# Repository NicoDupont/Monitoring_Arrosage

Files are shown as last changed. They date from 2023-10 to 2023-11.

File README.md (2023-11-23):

## Monitoring du circuit d'eau d'arrosage

# Montage réalisé sur une protoboard. un pcb dédié sera réalisé

Montage à base d'esp32 utilisé principalement pour monitorer le circuit d'arrosage.  

- pression
- temperature
- debitmetre/volume
- Ouverture/fermeture vanne motorisée  

### Fonctionnement :

Collecte des données.  
Les données remontent dans home-assistant via esphome.  
 => automatisme dans home-assistant   

### Liste des composants :

- 1x esp32 avec antenne wifi externe soudée sur connecteur sma (pas d'esp32u sous la main)
- 8x relais 5v (2x4) (alimente en 5v, logique en 3.3v)
- 1x alim 12v2A
- 1x convertisseur dc 12v=>5v
- 1x convertisseur dc 5v=>3.3v (ams1117)
- 2x BME280 (3.3v)
- 2x DS18B20 (3.3v)
- 1x resistance 4.7 Kohm
- 4x résistance 10 kohm
- 1x PCF8575 (3.3v)
- 1x ADS1115 (5v) + 1x level shifter (i2c 5v<=>3.3v)
- 3x Vannes motorisées 1" 12vdc avec retour d'info position (12v,cr702,bsp,manuel+indicateur) [vanne](https://fr.aliexpress.com/item/32960203891.html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)
- 3x Capteur pression 0.5/4.5v 0-100psi (5v) [pression](https://www.amazon.fr/gp/product/B08ZDLYKFH/ref=ox_sc_saved_image_1?smid=A1KGD9U4C0ZGWS&psc=1)
- 2 débimetres 1.5" YF-DN40 0-150L (5v) [debimetre](https://fr.aliexpress.com/item/1005003177939542.html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)
- Pcb, Bornier, Connecteur, entretoise, cavalier, support,Fusible, Porte Fusible, etc... 

### Cablage :

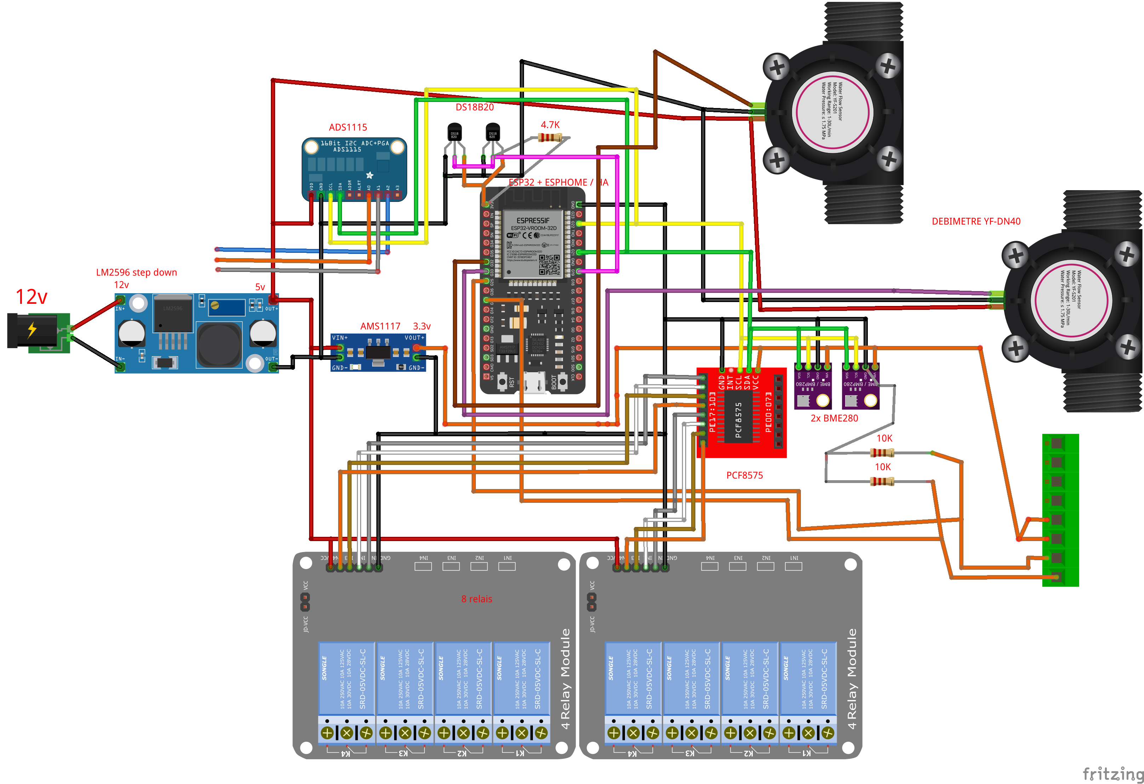
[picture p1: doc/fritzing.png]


### Montage :

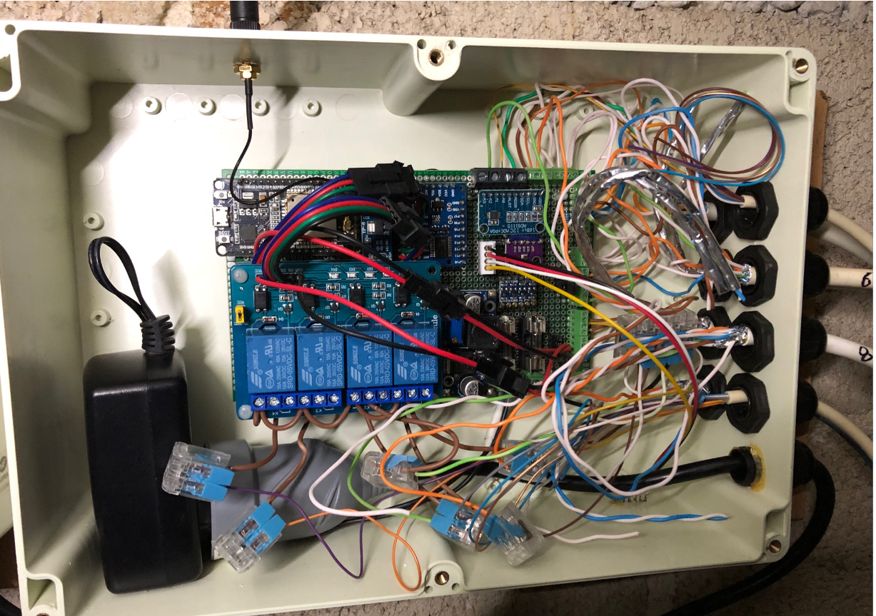
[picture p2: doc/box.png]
board


### HomeAssistant :

#### Esphome :

[yaml](https://github.com/NicoDupont/Monitoring_Arrosage/blob/main/esp-vs-arrosage.yaml)

#### Entités :

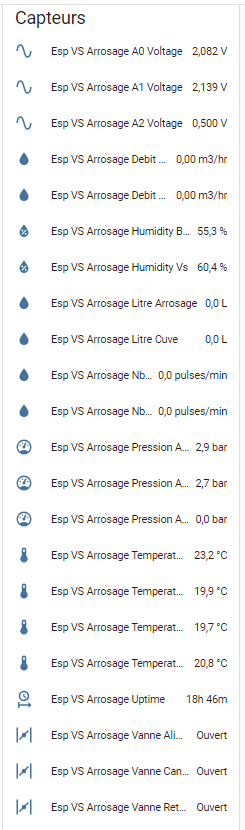
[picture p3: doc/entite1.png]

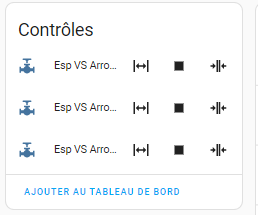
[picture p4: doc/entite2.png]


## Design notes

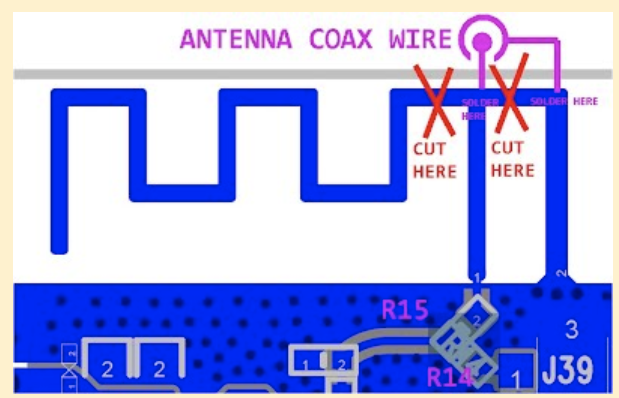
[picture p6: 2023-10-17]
doc/antenne_esp32.png

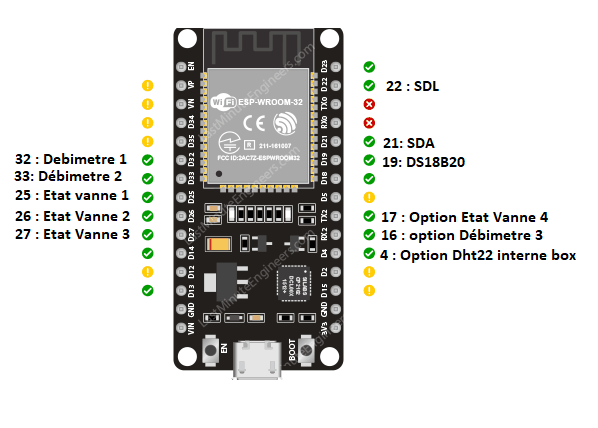
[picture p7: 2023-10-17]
doc/ESP32-GPIO-moni_arrosage.png

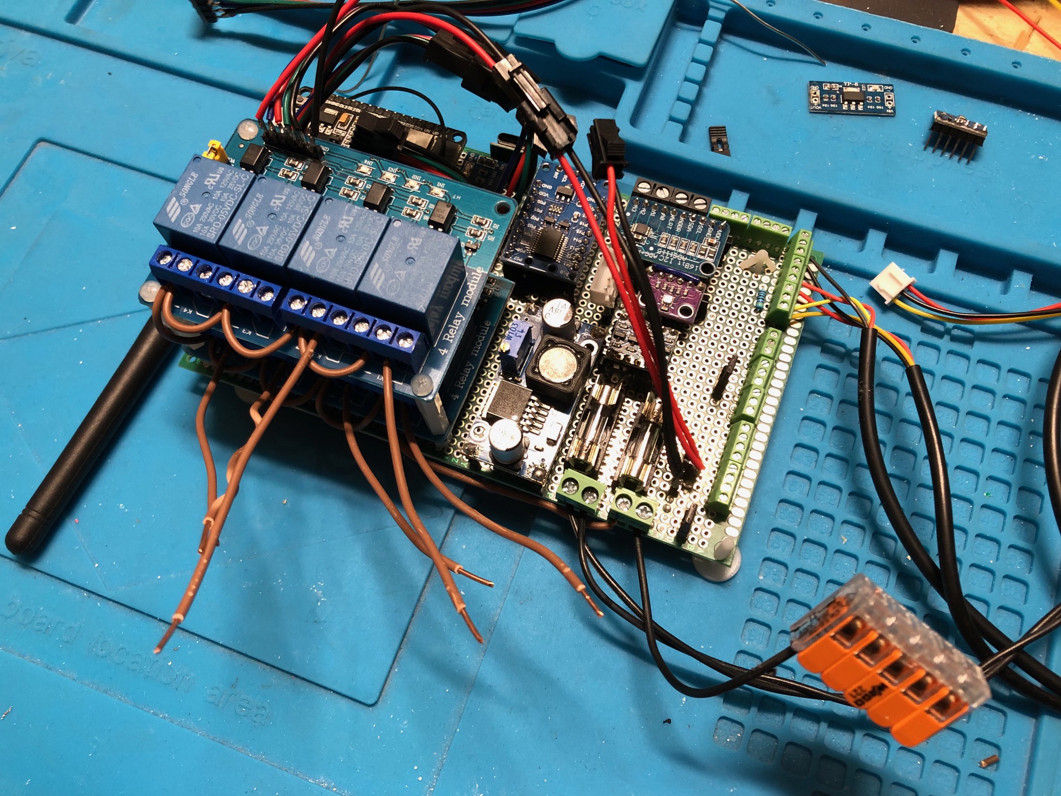
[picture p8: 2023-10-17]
doc/pcbok.jpg

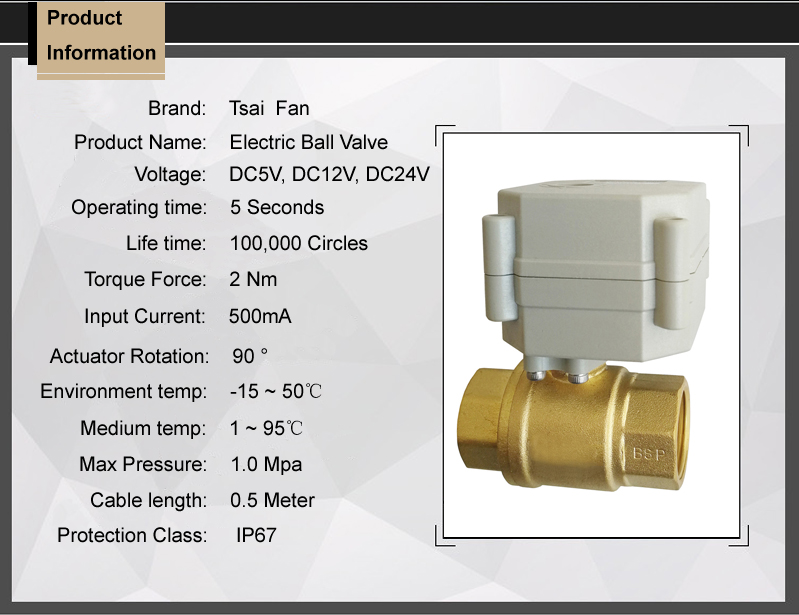
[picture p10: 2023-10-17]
doc/vanne1.jpg

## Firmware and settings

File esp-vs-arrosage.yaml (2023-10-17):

substitutions:
  friendly_name: "Esp VS Arrosage"
  friendly_name_wifiap: "Esp-VS-Arrosage-Hotspot"
  interval_update_court: "5s"
  interval_update_normal: "60s"
  interval_update_long: "600s"
  valve_duration: "5s"

esphome:
  name: esp-vs-arrosage
  comment: esp32 30pin monitoring temperature + pression + débimetre + gestion des vannes motorisées de la partie arrosage dans le vide sanitaire

esp32:
  board: esp32dev

# Enable logging
logger:

# Enable Home Assistant API
api:
#  encryption:
#    key: "a/cf+0bYDB1PlbJG8EkZfm23KiwYMVkIwHGuOpQmEqk="

ota:
  password: "001e0cad2c29a727973ae716dd966c53"

wifi:
  networks:
  - ssid: !secret wifi_maison_ssid
    password: !secret wifi_maison_password
  - ssid: !secret wifi_maison_2_ssid
    password: !secret wifi_maison_2_password
  reboot_timeout : 2min #reboot si pas de wifi actif

  # Enable fallback hotspot (captive portal) in case wifi connection fails
  ap:
    ssid: "${friendly_name_wifiap}"
    password: !secret wifi_esp_ap_password

captive_portal:

#--------------------------------------
#esp32_ble_tracker:
#bluetooth_proxy:

#--------------------------------------
web_server:
  port: 80
  version: 2

# ds18b20 temperature eau
dallas:
  - update_interval : ${interval_update_normal}
    pin: 19
    id: dallas_a
  
#i2c ads1115 + pcf8575 + bme280
i2c:
  sda: 21
  scl: 22
  scan: True
  id: bus_a

#i2c pcf8575 i/o extender 16 gpio pour gérer les 2 cartes 4 relais (3 vannes motorisées et donc 1 vanne possible en plus )
pcf8574:
  - id: 'pcf8575_hub'
    address: 0x20 #ou 0x21
    pcf8575: True

#i2c ads1115 pour lire les capteurs de pression 100psi 0.5=>4.5v
ads1115:
  - address: 0x48

time:
  - platform: homeassistant
    timezone: "Europe/Paris"
    id: ha_time

#----------------------------------------------------------------------------------------------
#----------------------------------------------------------------------------------------------
#binary_sensor
binary_sensor:

# ETAT VANNE MOTORISEE  
  - platform: gpio
    pin:
      number: 25
      inverted: true
    name: "${friendly_name} Vanne Canal Status"
    id: EspVsArrosageVanneCanalStatus
    device_class: opening

  - platform: gpio
    pin:
      number: 26
      inverted: true
    name: "${friendly_name} Vanne Alim Cuve Status"
    id: EspVsArrosageVanneAlimCuveStatus
    device_class: opening

  - platform: gpio
    pin:
      number: 27
      inverted: true
    name: "${friendly_name} Vanne Retour Cuve Status"
    id: EspVsArrosageVanneRetourCuveStatus
    device_class: opening

# DIAGNOSTIQUE
#--------------------------------------
#boolean status of the esp32
  - platform: status
    name: "${friendly_name} Status"
    id : EspVsArrosageStatus

text_sensor:
  - platform: template
    name: "${friendly_name} Uptime"
    id: uptime_human
    icon: mdi:clock-start 
#--------------------------------------
#wifi   
  - platform: wifi_info
    ip_address:
      name: "${friendly_name} Local IP"
      id : EspVsArrosageLocalIp
    ssid:
      name: "${friendly_name} SSID"
      id : EspVsArrosageSSID

#----------------------------------------------------------------------------------------------
#----------------------------------------------------------------------------------------------
#bouton
button:
  - platform: restart
    name: "${friendly_name} Restart"
    id : EspVsArrosageRestart
  - platform: shutdown
    name: "${friendly_name} Shutdown"
    id : EspVsArrosageShutdown
  - platform: safe_mode
    name: "${friendly_name} Safe Mode"
    id : EspVsArrosageSafeMode


#----------------------------------------------------------------------------------------------
#----------------------------------------------------------------------------------------------
#sensor
sensor:

#--------------------------------------
#esp32 temp
  - platform: internal_temperature
    name: "${friendly_name} Internal Esp32 Temp"
    id: EspVsArrosageInternalEsp32Temp
    update_interval: ${interval_update_normal}

#BME280
#monitoring de la temperature de la box avec l'electronique / alim / relais
  - platform: bme280
    temperature:
      name: "${friendly_name} Temperature Box"
      id: EspVsArrosageTempBox
      oversampling: 16x
      accuracy_decimals: 1
    pressure:
      name: "${friendly_name} Pression Atmo Box"
      id: EspVsArrosagePressionAtmoBox
      oversampling: 16x
      accuracy_decimals: 1
    humidity:
      name: "${friendly_name} Humidity Box"
      id: EspVsArrosageHumiBox
      accuracy_decimals: 1
      oversampling: 16x
    address: 0x77 #or 0x76/0x77
    i2c_id: bus_a
    update_interval: ${interval_update_normal}
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
